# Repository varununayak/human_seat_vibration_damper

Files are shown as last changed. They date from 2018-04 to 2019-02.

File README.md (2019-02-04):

# human_seat_vibration_damper
Design, fabrication, simulation and testing of a viscous dash-pot for a car seat vibration setup. 

This was a project that Varun worked on during his junior year of undergraduate studies at BITS Pilani, Goa Campus, in 2016-17.

Please have a look at the Documentation for theoretical foundations and the design. 

'ENDSemReport3-2.pdf' contains the piston and the vibration setup design (along with the electrodynamic shaker and the sensor-DAQ system) used for the system identification of a passive damper. This design project was further extended to create our very own magnetorhelogical damper. The report also lists three (unsuccessful) attempts to design and fabricate one.

'HumanSeatVibration.pdf' is a short assignment, as part of a course on vibrations and control, that models the dynamics of a seated human body and finds the resonant frequencies and mode shapes of excitation.

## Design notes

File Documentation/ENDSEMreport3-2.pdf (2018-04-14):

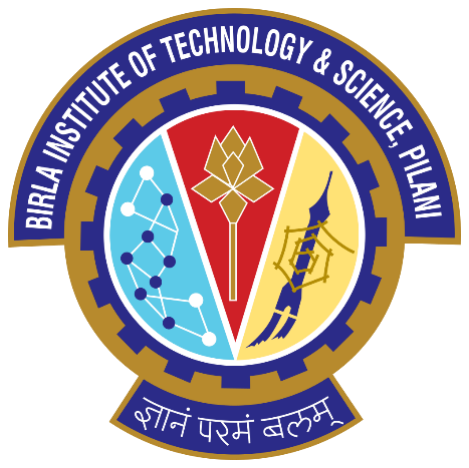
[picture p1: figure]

# SEMESTER REPORT

on

### “System Identification of MR Damper”

Prepared by
Nayak Varun Uday | 2014A4PS086G
Rishabh Chaturvedi | 2014A4PS298G
Shubhan Parag Patni | 2014A4PS154G

for

### Dr PM Singru

Department of Mechanical Engineering BITS Pilani K K Birla Goa Campus

# Acknowledgements

We would like to thank Dr PM Singru for his esteemed guidance throughout the course of this project. It has been a great learning experience for us to work under him at the Machine Dynamics Lab, BITS Pilani K K Birla Goa Campus

We would also like to thank the Workshop Instructors and Superintendent Mr Vijay Suryawanshi for their assistance and cooperation. They played a key role in the fabrication of our damper and setup.

# INDEX

i. Design of a cam to generate sinusoidal input vibration for seat ii. Conversion of Passive Damper to MR Damper (Attempt 1)
a. Setup
b. Use of magnetic particles (Magnaflux Spray) iii. Experimentation
a. Procedure
b. Results
c. Inferences
iv. Conversion of Passive Damper to MR Damper (Attempt 2)
a. Magnetic nano-particles
b. Old MR Damper
v. Experimentation
a. Response for Old MR Damper
b. Summary
vi. Conversion of Passive Damper to MR Damper (Attempt 3)
a. Design of a piston around which a current carrying coil can be wrapped
b. New Setup
vii. Experimentation
a. Procedure
b. Results
c. Inferences
viii. Conclusion

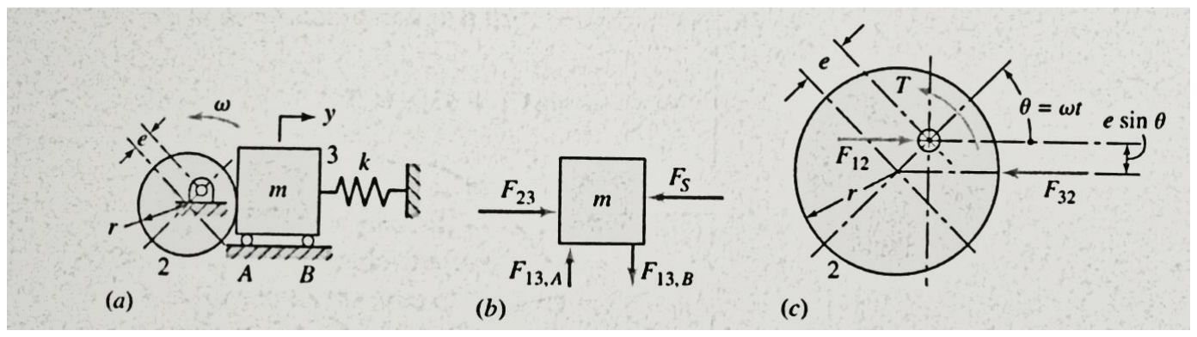
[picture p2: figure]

The CAM follower physical model

### Design of a cam to generate a sinusoidal input for a seat vibration setup

In order to take our studies on human body vibration analysis and ergonomics, we proposed to design a CAM which would generate a sinusoidal input to a seat attached to a follower.

Model-

An eccentric CAM was used as elaborate analytical solutions for its dynamics were available in literature. Also, it would generate the desired sinusoidal oscillatory motion at the output. The CAM would be accompanied by a flat-face follower as this design would be mechanically stronger and less complicated to design and fabricate given the various mechanical elements that are present in a roller follower.

CAM kinematics:

y = e − e cos ωt | ; | ẏ = eω sin ωt | ; | ÿ= eω

2
cos ωt

For the dynamic model, we assume that there is no friction and there is a preload P=kδ where δ is the preload compression given to the follower spring during installation.

Summing forces on the follower mass in the y-direction gives:

| ∑F
y = F23 − k(y + δ) = m ÿ

The force F23 is the contact force between the cam and the follower and hence can have only a positive value. Hence, substitution of the expression for y in the above equation of motion gives

F23 = (mω

2 − k)e cos ωt + (ke + P)

As the maximum probability of contact force becoming zero is at the top of the follower motion (ωt=180°), that value is substituted and F23 is made zero in order to find the value for k (minimum required value is obtained as this is the limiting case).

| | k = mω
| | 2 2e + δ

where

| | m = 100 kg (say) ω = 2π × 5 = 31.4 | rad

s

e = 0.01 cm
δ = 0.01 cm

Thesis values are arbitrary but conservative. Hence, substitution of these values gives:

k = 3287

kN
m

which is a very unrealistic value for a spring.

Let us assume that this spring is available and can be installed. However, we shall see in further calculations that the system parameters are far too unrealistic to be fabricated on the required scale.

Maximum value of F23 occurs at ωt=0, giving

F23(max) ≅ 132 kN

Maximum Torque required

Tmax ≅ 480 N. m

Maximum Power required

P ≅ 15 kW

These values are far too unrealistic to be implemented as anticipated and cannot be implemented with current constraints. As this is the most ideal model, we can safely assume that any other model would produce similar or worse results. The idea of using a cam for a human seat vibration setup is therefore terminated.

### Conversion of Passive Damper to MR Damper (Attempt 1)

Setup

To convert passive damper into active damper we required two modifications in our passive damper.

- To produce uniform magnetic field inside the cylinder of damper. This was achieved by using the basic principle of solenoid, electric current through the coil creates uniform magnetic field inside the coil. For this, we wound the outside of cylinder of damper with wire.

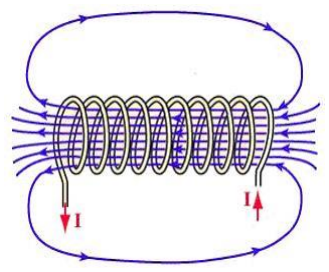
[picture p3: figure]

(Solenoid Magnetic Field)

Strength of magnetic field inside a solenoid is given by:

B =

μNI
L

B: Magnetic field.

µ: Permeability.

N: Number of coil turns (16 number of coil turns for our damper).

I: Current flowing through coil.

L: Length of coil (6cm for our damper).

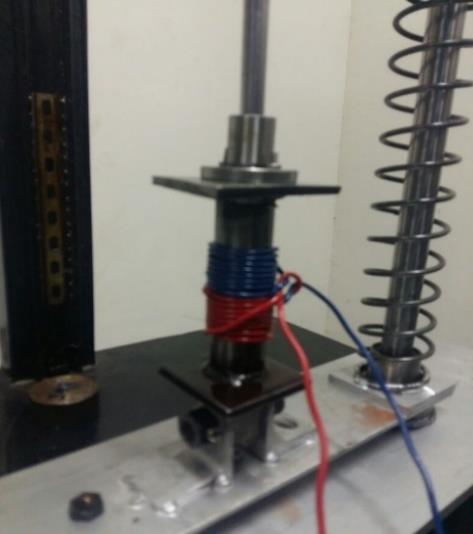
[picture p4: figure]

(Passive Damper converted to MR Damper)

Use of Magnaflux Spray

Secondly, the oil used inside the cylinder should be magnetized so that when it experiences magnetic field, there is change in viscosity of oil. For this purpose, Magnaflux spray used in Magnetic particle inspection for cracks and creeps was mixed with SAE-40 oil which is used in our passive damper and different concentrations of magnetized oil were prepared.

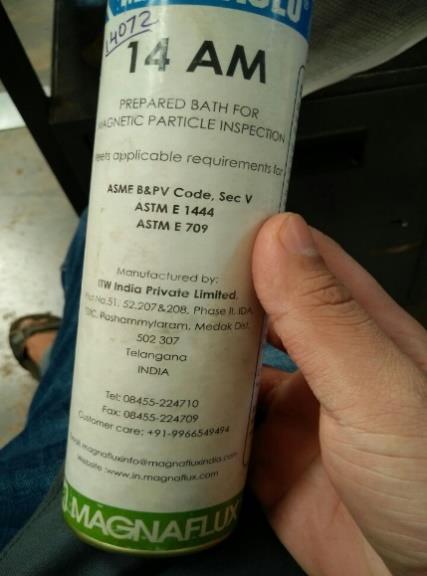
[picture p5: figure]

(Magnaflux Spray)

This kind of MR damper can be reverted back to passive damper anytime whenever required.

### Experimentation

MR dampers, like all magnetic materials, must possess a hysteresis curve. This curve can be represented between the current provided to the MR fluid, and its viscosity. Since the damping coefficient of a damper is directly proportional to the viscosity of the fluid inside it:

c = μ [
3πD

3
l
4d

3

(1 +

2d
D

)]

C is the damping coefficient, µ is the viscosity D, d and l are damper dimensions

A change in the current must produce corresponding changes in the damping provided by the damper. This is taken as a sufficient condition for the success of the experiment.

PROCEDURE

- Magnaflux-14 AM was added to SAE 40 Oil. All concentrations are measured as Wt./Wt. % The standard weight of oil taken = 118.27 g.
- Three concentrations were prepared. The shaker test was carried out for each of these currents while passing different amounts of current through a coil wrapped around the damper cylinder.
- A sine sweep test was carried out from 5Hz to 30Hz using constant displacement input from the shaker = 2 mm.

### 8.4% Magnaflux in SAE 40 Oil

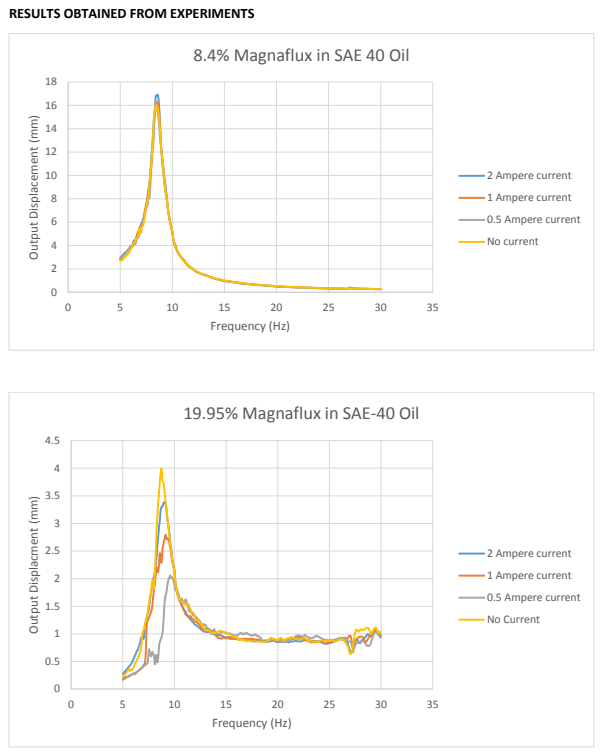
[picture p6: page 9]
Frequency (Hz); 2 Ampere current; 1 Ampere current; 0.5 Ampere current; No current; No Current

RESULTS OBTAINED FROM EXPERIMENTS

Output Displacement (mm)

19.95% Magnaflux in SAE-40 Oil

Output Displacment (mm)

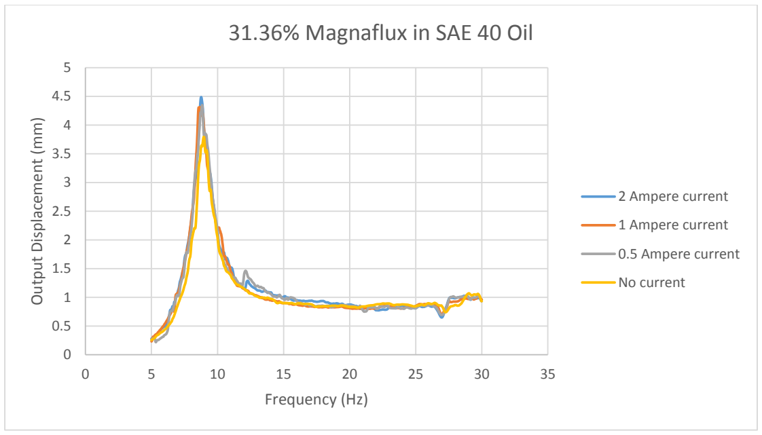
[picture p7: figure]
Output Displacement (mm); Frequency (Hz); 31.36% Magnaflux in SAE 40 Oil; 2 Ampere current; 1 Ampere current; 0.5 Ampere current; No current

INFERENCES

- No substantial change can be seen in the resonating frequencies of the system upon changing the current.
- Similarly, no change is observed in the resonating frequency upon change in concentration.
- There should have been a change in the resonating frequency if the damping of the system was changing due to varying currents. Therefore we can conclude that the damper, upon addition of Magnetic Inspection fluid, and with current passing around the cylinder, DOES NOT behave as an active MR Damper.
There could have been two major reasons for this failure:
- Magnetic Shielding occurs. Since the coil is wrapped outside the cylinder, the fluid (and therefore the magnetic particles) might be shielded by the effects of the solenoid by the cylinder material (Mild Steel).
- The concentration of magnetic particles might be very low to have any significant effect on the damping. The Magnaflux-14 AM only has a 5% proportion of particles to petroleum suspension. Therefore, when we add a portion of Magnaflux-14 AM to the SAE 40 oil, the proportion of magnetic particles introduced into the oil is very low. Thus, the question arises if there is a particular ‘threshold’ concentration beyond which magnetic particles have a significant effect on the viscosity of the MR fluid.

### Conversion of Passive Damper to MR Damper (Attempt 2)

Magnetic Nano-Particles

Magneto Rheological fluid

Electro-rheological (ER) fluid changes viscosity when an electric current is applied directly to the fluid itself. ER fluid was first invented and patented in the 1940s, and to varying degrees, development has continued ever since. It has been tested in a wide range of applications, from torque converters, clutches (http://www.formula1-dictionary.net/clutch.html) and dampers to synthetic muscles and dampers in powered prosthetic arms and legs. It works, but its shear strength (its resistance to shearing movement) is limited. Despite huge investments in research and development, ER fluid is still far from ready for any practical applications.

Magneto-rheological (MR) fluid on other side has shear strength about 10 times stronger than ER fluid. Invented at the same time as ER fluid, the two have many similarities. Both can use oil, silicone, water or glycol as the base fluid, and both contain polarizable particles suspended in the fluid. Polarizable means the particles can be forced to align in a specific way. These suspended polarizable particles are the basic difference between ER and MR fluids. ER fluid uses particles that polarize when directly exposed to an electric current. MR fluid uses somewhat larger particles of iron that polarize when surrounded by a magnetic field.

Our Approach

Fe³⁺ ions were created using the chemical reaction of Fe(OH)3 and HCL. Two types of Iron particles were used purified iron particles and unpurified iron particles. Three different concentrations were made. One with pure particles having concentration 7.5% by weight of pure iron particles in SAE 40 oil, other with impure iron particles having concentration 8.75% by weight of impure iron particles in SAE 40 oil. These two concentrations were used while conducting test with old model of MR Damper having coil wound around cylinder.

Below are the tables describing the observations made while making the above mixture of magnetized fluid:

Old MR Damper (impure Particles)
weight of empty bottle (g) | 19.87
Bottle + Particles (g) | 22.89
Weight of Particles (g) | 3.02
Weight of Bottle + Oil + Particle (g) | 63.11
Weight of Oil (g) | 40.22
Wt/Wt % of oil | 7.508702

Old MR Damper (Pure iron particles)
Empty Bottle Weight (g) | 21.07
Bottle + Particles (g) | 22.17
Particle Wt. (g) | 1.1
Bottle + Particles + Oil (g) | 34.74
Oil (g) | 12.57
Wt./Wt. % | 8.750994

### Experimentation

Test 1: 7.5% wt/wt rough nanoparticles

Sweep Sine Responses for the above concentration are given below.

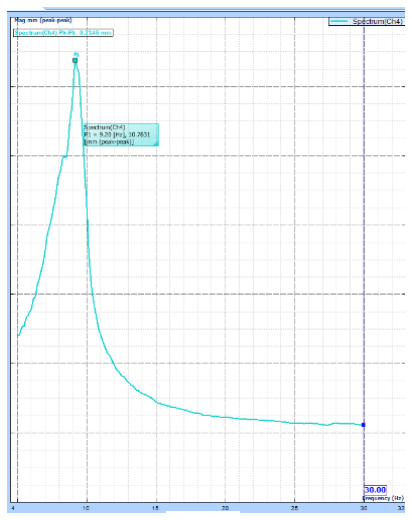
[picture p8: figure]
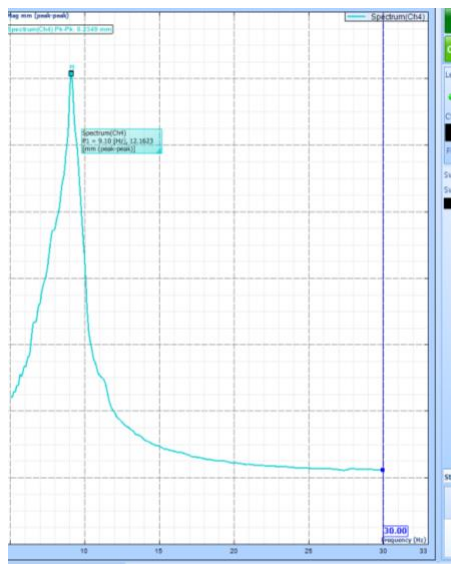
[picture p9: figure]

0A | 0.5A

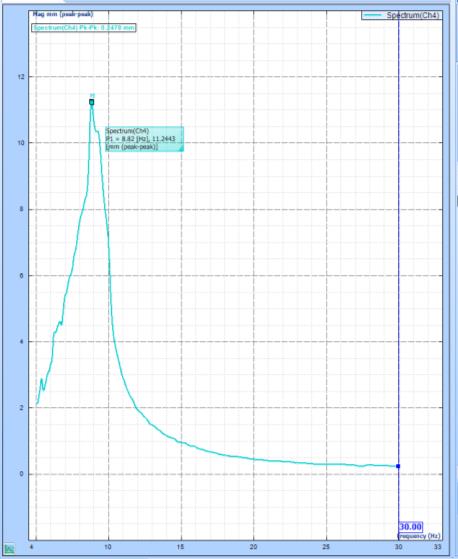
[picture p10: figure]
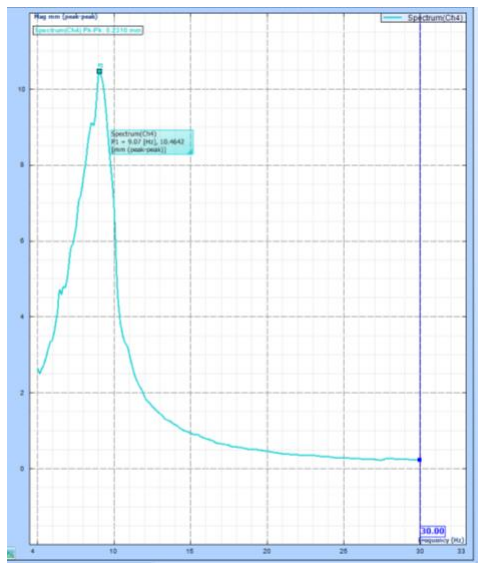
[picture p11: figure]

1A | 2A

Test 2: 8.75% wt/wt rough nanoparticles

Sweep Sine Responses for the above concentration are given below.

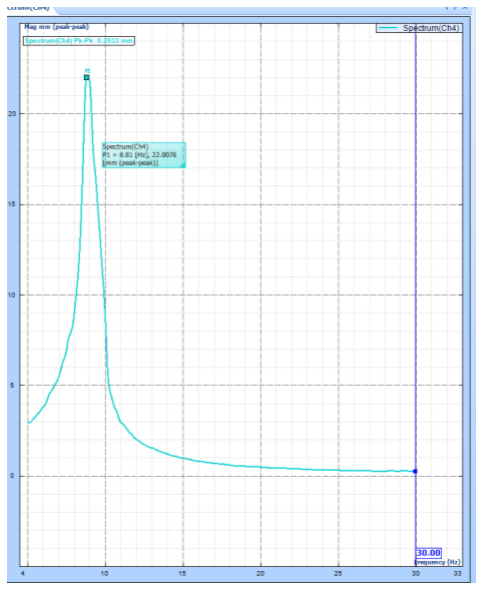
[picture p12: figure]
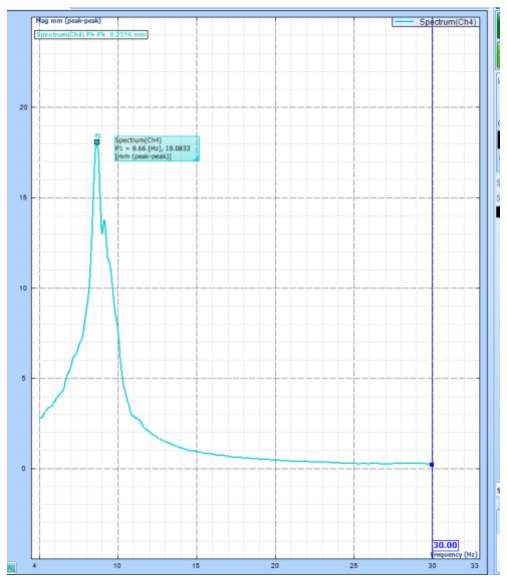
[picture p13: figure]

0A | 0.5A

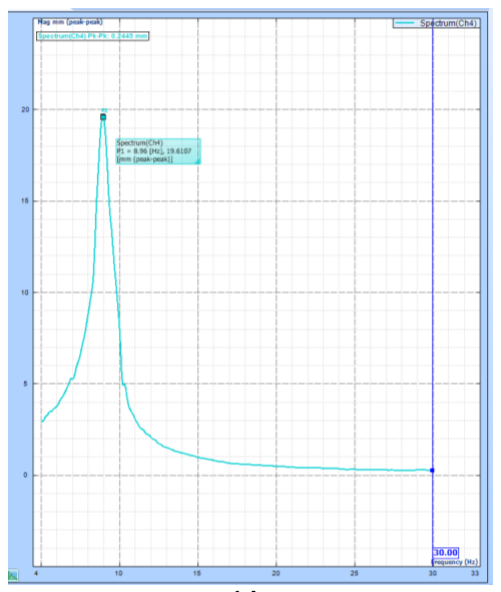
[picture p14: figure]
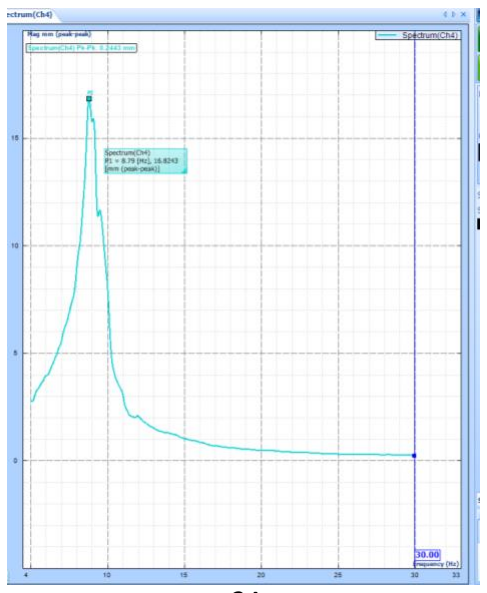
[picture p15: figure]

1A | 2A

Summary of Results

For the old MR damper setup and nano particles, following were the results.:

Current | Unrefined Particles | Refined Particles
0 Ampere | 9.2 Hz | 8.66 Hz
0.5 Ampere | 9.1 Hz | 8.81 Hz
1 Ampere | 8.8 Hz | 8.96 Hz
2 Ampere | 9.07 Hz | 8.79 Hz

### Conversion of Passive Damper to MR Damper (Attempt 3)

Design of a piston around which current-carrying coil can be wrapped

By our current experimentation with the new mixture of oil and magnetic particles, there has been no change in the damping constant of the system for current varying between 0-2A. Therefore, there is a possibility that the magnetic field experienced by the fluid is not strong enough due to the shielding effect of the steel cylinder.
Thus, a new design of the piston in which the current-carrying coil would be wrapped around the piston was to be created.

Points to be taken care of for this design-

1. The groove made in the piston should be of appropriate dimensions so that the piston surface is kept as flat as possible. The safe wire diameter required for this specified order of current is about 0.8 to 1.2mm. Hence the groove depth was decided to be fixed at 1mm.
2. Since there will be wiring coming out of the inside of the cylinder, there should be appropriate arrangements in the sealing made for the same.
3. Overall sealing should be made tight as magnetic nanoparticles are expensive and leakage cannot be afforded. The need for sealing was eliminated in this iteration of design by extending the piston further into the cylinder hence keeping a healthy clearance (about 2cm more than the passive damper) between the upper surface of the fluid and the cylinder opening.

The piston outer diameter was fixed at 17mm and shaft diameter at 10mm (following the passive damper dimensions).

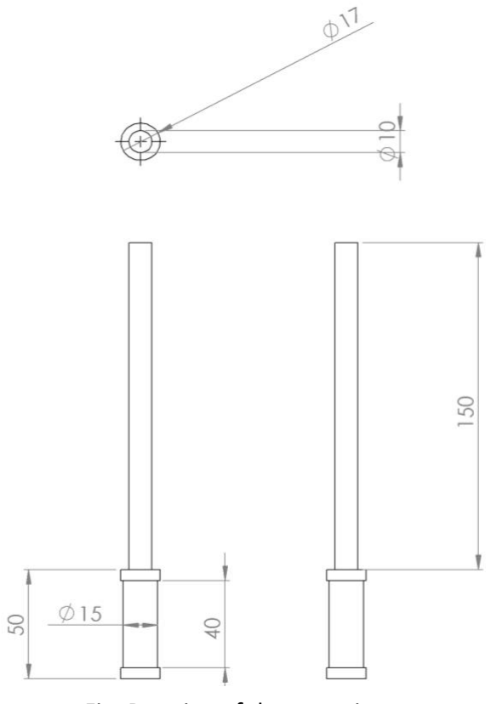
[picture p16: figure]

Fig: Drawing of the new piston

Fabrication of the New Piston

New Piston for the MR Damper was manufactured on Lathe machine carried out in our workshop.

Equipment Used: 25mm MS solid cylinder rod of 30cm length (issued from workshop), Lathe Machine, Vernier Caliper, Flat fine file, Emery paper, 8mm winding wire, feviquick.

Required dimensions of piston: 170mm length of shaft, 50mm length of piston, 10mm diameter of shaft, 17 mm diameter of piston at the ends with 4mm length at each end, middle part of piston is made to be of 15.8mm diameter with its length to be 42mm.

10mm diameter of shaft passes through the linear bearing to keep it centric with the cylinder and tight fits into the upper connector which has hole for the same of 10mm depth 10mm diameter. Linear bearing is screwed on the upper plate of cylinder containing magnetized fluid.

Procedure followed for manufacturing:

- 30mm MS solid cylinder rod of 300mm length is taken a 5mm hole is drilled at one of the faces of MS rod so as to reduce the wobbling by holding the rod in chuck and tailstock of Lathe machine.
- Carrying out the turning operation to reduce diameter from 25 mm to 17mm for 240mm of length of work piece from one end.
- Further carrying out turning operation to reduce 17mm diameter to 10mmdiameter for 180mm of length from the same end.
- To get the middle part of piston from 17mm to 15.8mm, it is machined from 184mm to 234mm from the same end.
- Parting tool is used on both the ends to get the final length of piston and shaft to 220mm as required.
- Winding wire was wound around the middle part of piston with 64 turns.
- Feviquick was used to make sure winding wire is glued to piston and doesn’t loosen up.
- Two ends of the winding wires come out from one of the screw holes of linear bearing out of the cylinder.
Dimension | DESIGN (mm) | ACTUAL (mm)
Piston Diameter (inner) | 15 | 15.4
Piston Diameter (outer) | 17 | 17.1

Table: Piston Dimensions

Setup

For new MR Damper 6.04% by weight of pure iron particles in SAE 40 oil was used. Multiple readings were taken for different value of the current 0, 0.5, 1, 1.5, 2 Amperes.

New MR Damper (Pure iron particles)
Weight of empty bottle(g) | 19.18
Weight of bottle + oil(g) | 75.28
Weight of bottle + oil + particles(g) | 78.67
Weight of Oil(g) | 56.1
Weight of Particles(g) | 3.39
Concentration Wt/Wt(%) | 6.042781

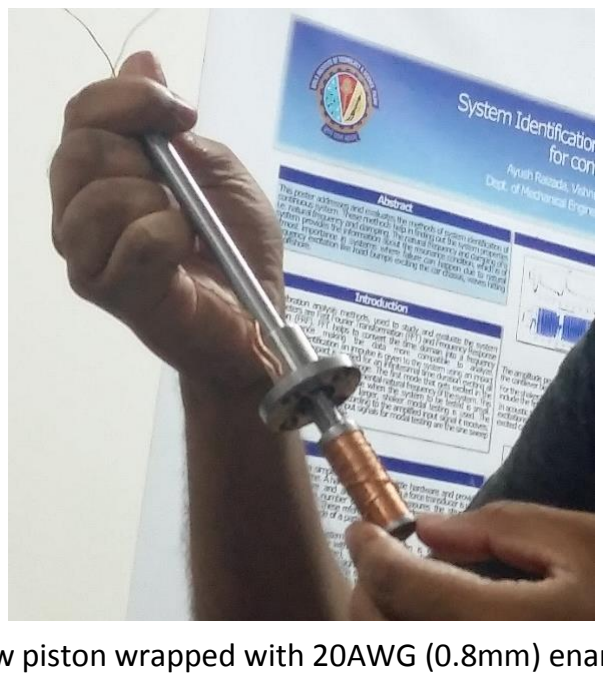
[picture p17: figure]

Fig: The new piston wrapped with 20AWG (0.8mm) enamelled wire

### Experimentation

### No Current

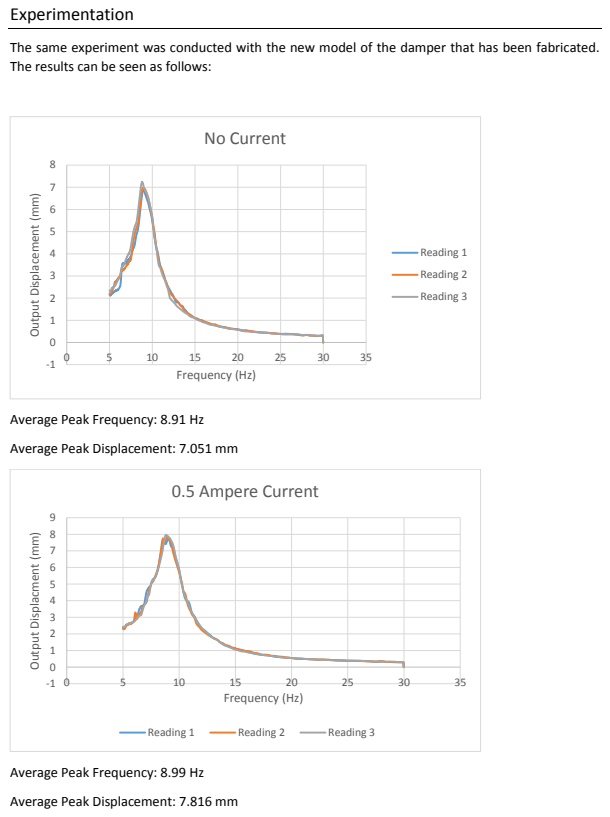
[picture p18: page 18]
Frequency (Hz); Reading 1; Reading 2; Reading 3; 0.5 Ampere Current

The same experiment was conducted with the new model of the damper that has been fabricated.
The results can be seen as follows:

Output Displacement (mm)

Average Peak Frequency: 8.91 Hz

Average Peak Displacement: 7.051 mm

Output Displacment (mm)

Average Peak Frequency: 8.99 Hz

Average Peak Displacement: 7.816 mm

### 1 Ampere Current

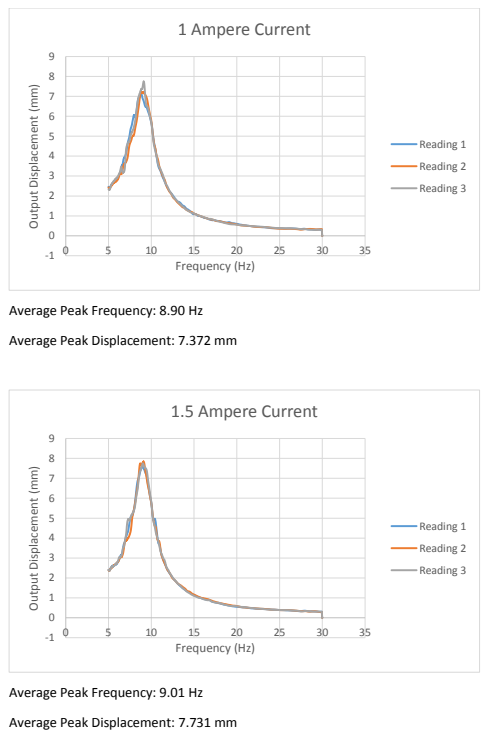
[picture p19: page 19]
Frequency (Hz); Reading 1; Reading 2; Reading 3; 1.5 Ampere Current

Output Displacement (mm)

Average Peak Frequency: 8.90 Hz

Average Peak Displacement: 7.372 mm

Average Peak Frequency: 9.01 Hz

Average Peak Displacement: 7.731 mm

### 1.91 Ampere Current

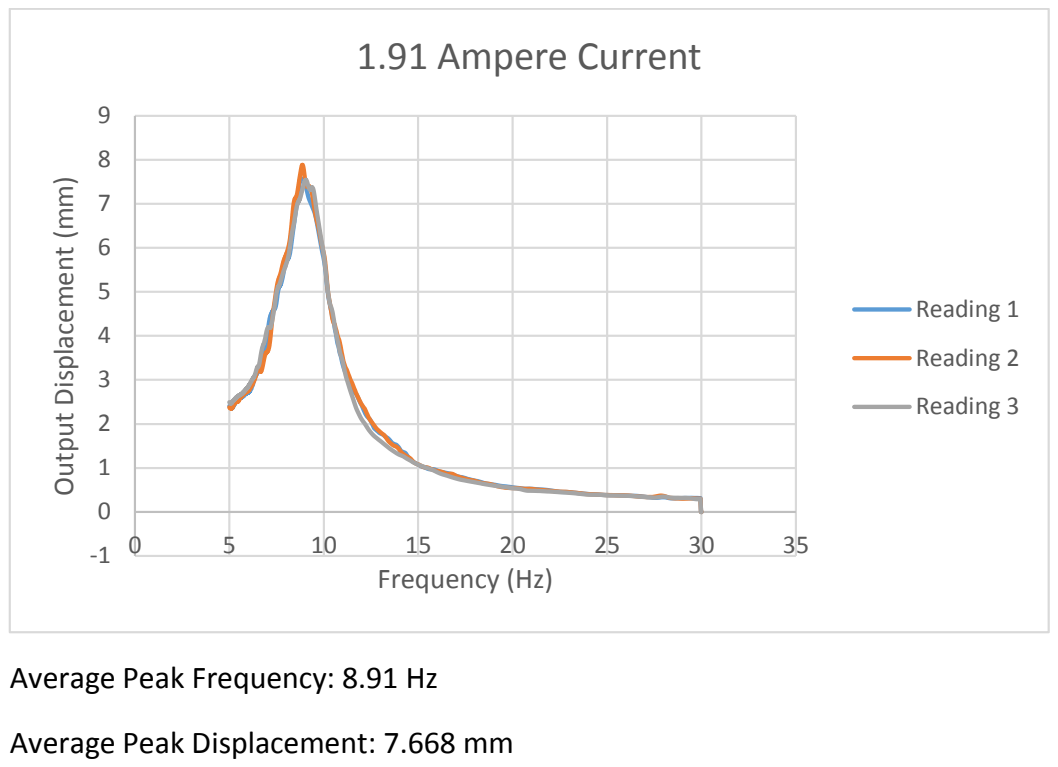
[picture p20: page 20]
Frequency (Hz); Reading 1; Reading 2; Reading 3

Output Displacement (mm)

Average Peak Frequency: 8.91 Hz

Average Peak Displacement: 7.668 mm

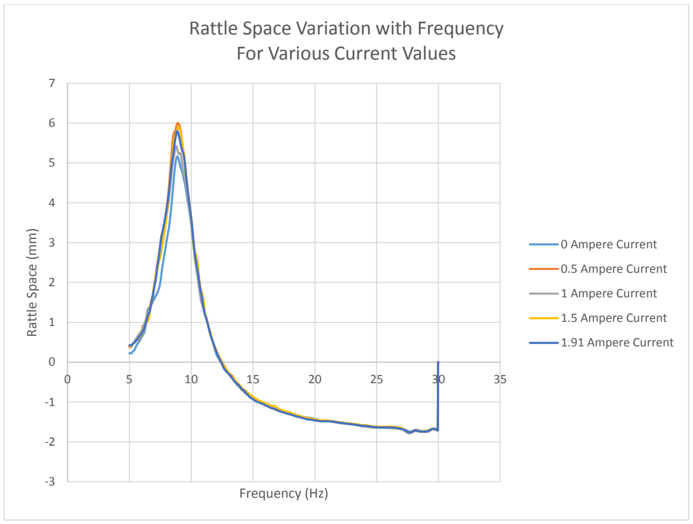
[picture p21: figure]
Rattle Space (mm); Frequency (Hz); Rattle Space Variation with Frequency For Various Current Values; 0 Ampere Current; 0.5 Ampere Current; 1 Ampere Current; 1.5 Ampere Current; 1.91 Ampere Current

Although there is slight variation of the resonant frequency, it is not uniform, nor can any predictable pattern be observed. The variation can simply be attributed to arise from experimental errors, which would not be present in an ideal scenario. Thus the attempt to construct an inexpensive MR Damper has failed.

Possible Reasons for failure:

1. The ferromagnetic particles are heavy. They do not float in the oil but rather settle down to the bottom of the cylinder and therefore no effect can be observed on the fluid’s viscosity.
2. The number of turns on the piston may not be enough to generate a field strong enough to magnetise the fluid and affect its viscosity.

Further:

A surfactant such as oleic acid, or more commonly a detergent, can be added to the oil. This will increase the surface tension of the fluid and prohibit the particles from settling down.

Better methods for obtaining/purifying of particles can be used so that the particles are finer and lighter.

### Conclusion

After successfully designing, fabricating and testing the passive damper, the objective of this semester’s work was to design and fabricate a low-cost active damper. After gathering the required materials and exhaustive experimentation, a total of three attempts were possible in the stipulated time. Unfortunately, the results indicate that the attempts were unsuccessful.

However, there still exists a good possibility of ensuring active response from the setup by following the suggestions mentioned above as well as further research on MR damper technology.

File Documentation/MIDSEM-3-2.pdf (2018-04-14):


# MID-SEMESTER REPORT

on

### “System Identification of MR Damper”

Prepared by
Nayak Varun Uday | 2014A4PS086G
Rishabh Chaturvedi | 2014A4PS298G
Shubhan Parag Patni | 2014A4PS154G

for

### Dr PM Singru

Department of Mechanical Engineering BITS Pilani K K Birla Goa Campus

# INDEX

i. Design of a cam to generate sinusoidal input vibration for seat
ii. | Conversion of Passive Damper to MR Damper
iii. | Attempt to convert passive damper to active damper by introduction of magnetic particles in damper oil
a. Procedure
b. Results
c. Inferences
d. Further Iterations
iv. Design of a piston around which a current carrying coil can be wrapped


The CAM follower physical model

### Design of a cam to generate a sinusoidal input for a seat vibration setup

In order to take our studies on human body vibration analysis and ergonomics, we proposed to design a CAM which would generate a sinusoidal input to a seat attached to a follower.

Model-

An eccentric CAM was used as elaborate analytical solutions for its dynamics were available in literature. Also, it would generate the desired sinusoidal oscillatory motion at the output. The CAM would be accompanied by a flat-face follower as this design would be mechanically stronger and less complicated to design and fabricate given the various mechanical elements that are present in a roller follower.

CAM kinematics:

y = e − e cos ωt | ; | ẏ = eω sin ωt | ; | ÿ= eω

2
cos ωt

For the dynamic model, we assume that there is no friction and there is a preload P=kδ where δ is the preload compression given to the follower spring during installation.

Summing forces on the follower mass in the y-direction gives:

| ∑F
y = F23 − k(y + δ) = m ÿ

The force F23 is the contact force between the cam and the follower and hence can have only a positive value. Hence, substitution of the expression for y in the above equation of motion gives

F23 = (mω

2 − k)e cos ωt + (ke + P)

As the maximum probability of contact force becoming zero is at the top of the follower motion (ωt=180°), that value is substituted and F23 is made zero in order to find the value for k (minimum required value is obtained as this is the limiting case).

| | k = mω
| | 2 2e + δ

where

| | m = 100 kg (say) ω = 2π × 5 = 31.4 | rad

s

e = 0.01 cm
δ = 0.01 cm

Thesis values are arbitrary but conservative. Hence, substitution of these values gives:

k = 3287

kN
m

which is a very unrealistic value for a spring.

Let us assume that this spring is available and can be installed. However, we shall see in further calculations that the system parameters are far too unrealistic to be fabricated on the required scale.

Maximum value of F23 occurs at ωt=0, giving

F23(max) ≅ 132 kN

Maximum Torque required

Tmax ≅ 480 N. m

Maximum Power required

P ≅ 15 kW

These values are far too unrealistic to be implemented as anticipated and cannot be implemented with current constraints. As this is the most ideal model, we can safely assume that any other model would produce similar or worse results. The idea of using a cam for a human seat vibration setup is therefore terminated.

### Conversion of Passive Damper to MR Damper

To convert passive damper into active damper we required two modifications in our passive damper.

- Firstly, to produce uniform magnetic field inside the cylinder of damper. This was achieved by using the basic principle of solenoid, electric current through the coil creates uniform magnetic field inside the coil. For this, we wound the outside of cylinder of damper with wire.

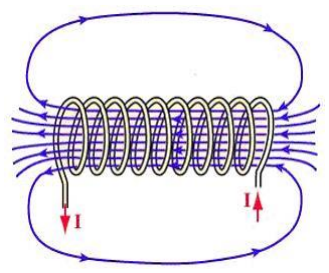
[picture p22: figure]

(Solenoid Magnetic Field)

Strength of magnetic field inside a solenoid is given by:

B =

μNI
L

B: Magnetic field.

µ: Permeability.

N: Number of coil turns (16 number of coil turns for our damper).

I: Current flowing through coil.

L: Length of coil (6cm for our damper).

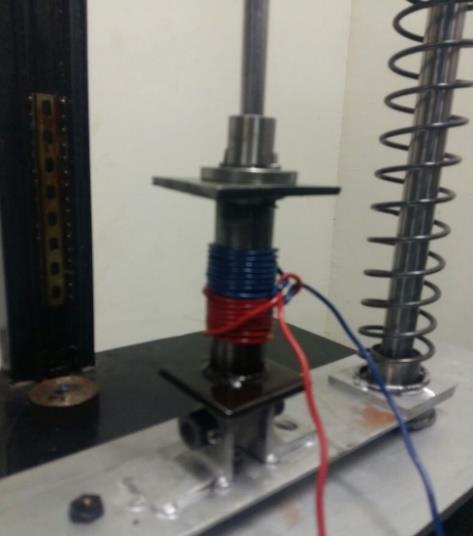
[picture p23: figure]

(Passive Damper converted to MR Damper)

- Secondly, the oil used inside the cylinder should be magnetized so that when it experiences magnetic field, there is change in viscosity of oil. For this purpose, Magnaflux spray used in

Magnetic particle inspection for cracks and creeps was mixed with SAE-40 oil which is used in our passive damper and different concentrations of magnetized oil were prepared.


(Magnaflux Spray)

This kind of MR damper can be reverted back to passive damper anytime whenever required.

Problem with this MR Damper

- There is a possibility that cylinder’s thickness will shield the magnetic field produced inside the cylinder. We haven’t been able to confirm that magnetic shielding exists and if it exists then what is the strength of magnetic field produced inside the cylinder.
- It cannot be assured that mixing SAE 40 oil with Magnaflux spray will result in magnetized oil.

Alternative approach

To encounter the problem that exists with this revertible MR damper this alternative approach is being considered.

- We need to manufacture another piston onto which the wire will be wound around as done in standard MR dampers this will eliminate shielding of magnetic field.
- SAE 40 oil can be mixed with Nano magnetic particles to get magnetized oil for MR damper.

### Experiment: Attempt to convert passive damper to active damper by

introduction of Magnetic Particles into damper oil.

MR dampers, like all magnetic materials, must possess a hysteresis curve. This curve can be represented between the current provided to the MR fluid, and its viscosity. Since the damping coefficient of a damper is directly proportional to the viscosity of the fluid inside it:

c = μ [
3πD

3
l
4d

3

(1 +

2d
D

)]

C is the damping coefficient, µ is the viscosity D, d and l are damper dimensions

A change in the current must produce corresponding changes in the damping provided by the damper. This is taken as a sufficient condition for the success of the experiment.

PROCEDURE

- Magnaflux-14 AM was added to SAE 40 Oil. All concentrations are measured as Wt./Wt. % The standard weight of oil taken = 118.27 g.
- Three concentrations were prepared. The shaker test was carried out for each of these currents while passing different amounts of current through a coil wrapped around the damper cylinder.
- A sine sweep test was carried out from 5Hz to 30Hz using constant displacement input from the shaker = 2 mm.

### 8.4% Magnaflux in SAE 40 Oil

Frequency (Hz); 2 Ampere current; 1 Ampere current; 0.5 Ampere current; No current; No Current

RESULTS OBTAINED FROM EXPERIMENTS

Output Displacement (mm)

19.95% Magnaflux in SAE-40 Oil

Output Displacment (mm)

Output Displacement (mm); Frequency (Hz); 31.36% Magnaflux in SAE 40 Oil; 2 Ampere current; 1 Ampere current; 0.5 Ampere current; No current

INFERENCES

- No substantial change can be seen in the resonating frequencies of the system upon changing the current.
- Similarly, no change is observed in the resonating frequency upon change in concentration.
- There should have been a change in the resonating frequency if the damping of the system was changing due to varying currents. Therefore we can conclude that the damper, upon addition of Magnetic Inspection fluid, and with current passing around the cylinder, DOES NOT behave as an active MR Damper.
There could have been two major reasons for this failure:
- Magnetic Shielding occurs. Since the coil is wrapped outside the cylinder, the fluid (and therefore the magnetic particles) might be shielded by the effects of the solenoid by the cylinder material (Mild Steel).
- The concentration of magnetic particles might be very low to have any significant effect on the damping. The Magnaflux-14 AM only has a 5% proportion of particles to petroleum suspension. Therefore, when we add a portion of Magnaflux-14 AM to the SAE 40 oil, the proportion of magnetic particles introduced into the oil is very low. Thus, the question arises if there is a particular ‘threshold’ concentration beyond which magnetic particles have a significant effect on the viscosity of the MR fluid.

FURTHER ITERATIONS

- Introduction of Fe³⁺ particles into the damper oil. As we are directly introducing particles instead of a suspension, the concentration will be sharper.
- Wrapping the current carrying coil inside the damper by wrapping it around the piston. This will help in eliminating magnetic shielding as a reason for no change in the response of the system.

### Design of a piston around which current-carrying coil can be wrapped

By our current experimentation with the new mixture of oil and magnetic particles, there has been no change in the damping constant of the system for current varying between 0-2A. Therefore, there is a possibility that the magnetic field experienced by the fluid is not strong enough due to the shielding effect of steel.

Thus, a new design of the system in which the current-carrying coil will be wrapped around the piston will have to be designed.

Points to be taken care of for this design-

1. The groove made in the piston should be of appropriate dimensions so that the piston surface is kept as flat as possible
2. Since there will be wiring coming out of the inside of the cylinder, there should be appropriate arrangements in the sealing made for the same.
3. Overall sealing should be made tight as magnetic nanoparticles are expensive and leakage cannot be afforded

The project will proceed further with the design, fabrication and testing of the MR Damper equipped with such a piston. However, before we proceed, we will check whether our assumption of shielding is actually true or not by checking the magnetic field developed inside the cylinder with the current design configuration.

Proposed Piston Design

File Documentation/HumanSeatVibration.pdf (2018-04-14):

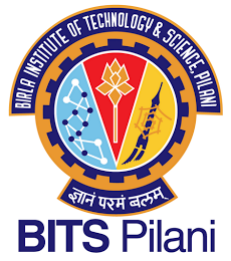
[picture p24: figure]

# Mode Shape Determination of a Dynamic Model of a Human Body in Seated Position

## Varun Uday Nayak ID: 2014A4PS086G

A project presented for partial fulfilment of the requirements of the course Mechanical Vibrations

## Department of Mechanical Engineering BITS Pilani, K K Birla Goa Campus

## Contents

1 Introduction | 2
2 Literature Used | 2
3 Human Body Model | 3
4 Equation of Motion | 4
5 Mode Shapes | 5
6 MATLAB Code | 6
7 Conclusion | 7
8 References | 7

1

## Mode Shape Determination of a Dynamic Model of a Human Body in Seated Position

Varun Uday Nayak
ID Number: 2014A4PS086G

Birla Institute of Technology and Science, Pilani - K K Birla Goa Campus

April 25, 2017

## 1 Introduction

The human body is subject to forces and displacements in everyday life: while one exercises, while one sits inside a moving car, while one performs manual labour and numerous other scenarios. Studying the dynamics of a human body has become an interesting topic of research in domains such as ergonomics, biomechanics, prosthetics, rehabilitation robotics and human-machine interaction. Since the human body is a complicated system, it had always been difficult to model it using simple analytical techniques. With improvements in computational techniques and rapid development in the field of biomechanics, it has become possible to accurately model such systems. Experimental testing has also evolved significantly due to the use of bio-instrumentation and carefully controlled dynamic environments.

## 2 Literature Used

A lot of research has been carried out in the domain of seat vibration models of a human body among other configurations. Behari and Noga [1] have developed five different biodynamic models of a seated human body and have analysed the transmissibility of seat vibrations onto the head. They have provided comprehensive anatomical data and have plotted results that give us an idea of the effect of frequency on the head transmissibility. Amar Kishore et al [3] have also done a transmissibility analysis of a seated human, specifically in the low frequency region. This makes prefect sense for regular car and bus commute on non-ideal roads. The model in this paper has most of its roots in the model presented in their paper due to its simplicity and effectiveness. Ksiazek and Lacny [4] have studied a 2-DOF active human body model with two distinct seat positions and analysed response due to impulse inputs. Liang and Chiang [2] have presented a rather complicated model of a human body considering all possible joints and have tabulated the results for seat-to-head transmissibility like [1] and [3].

2

## 3 Human Body Model


Figure 1: 5-DOF Seated Human Body Biomechanical Model

The human body can be modelled as a 5-DOF system as shown below. Note that as the objective of this paper is to develop a biomechanical model of a human body on a vibrating seat in vertical direction only, the masses have been lumped in a manner which results out of the consideration of only that direction. The abdomen has been assumed to be not connected to the back directly. The lower body and the pelvis have been merged into one to avoid the complexities involving joints in the leg and feet. Also, the feet have been assumed to be placed (fixed) flat on the ground. This model is a a great model for seat vibration analysis of a human body.

3

## 4 Equation of Motion

Applying Force Balance on (1)Pelvis and Lower Body (2)Abdomen (3)Upper Torso (4)Back and (5)Head, we get

m1x¨1 + ˙x1(c1 + c2 + c4 + c6) + ˙x2(−c2) + ˙x4(−c4) + x1(k1 + k2 + k4 + k6) + x2(−k2) + x4(−k4) = 0 (1) m2x¨2 + ˙x2(c2 + c3) + ˙x1(−c2) + ˙x3(−c3) + x2(k2 + k3) + x1(−k2) + x3(−k3) = 0 (2) m3x¨3 + ˙x3(c3 + c7) + ˙x2(−c3) + ˙x4(−c7) + x3(k3 + k7) + x2(−k3) + x4(−k7) = 0 (3) m4x¨4 + ˙x4(c4 + c5 + c7) + ˙x3(−c7) + ˙x1(−c4) + ˙x5(−c5) + x4(k4 + k5 + k7) + x3(−k7) + x1(−k4) + x5(−k5) = 0 (4) m5x¨5 + ˙x5(c5) + ˙x4(−c5) + x5(k5) + x4(−k5) = 0 (5)

In matrix form
m1 | 0 | 0 | 0 | 0
0 | m2 | 0 | 0 | 0
0 | 0 | m3 | 0 | 0
0 | 0 | 0 | m4 | 0
0 | 0 | 0 | 0 | m5

X¨ +

c1 + c2 + c4 + c6 | −c2 | 0 | −c4 | 0
−c2 | c2 + c3 | −c3 | 0 | 0
0 | −c3 | c3 + c7 | −c7 | 0
−c4 | 0 | −c7 | c4 + c5 + c7 | −c5
0 | 0 | 0 | −c5 | c5

X˙

+

k1 + k2 + k4 + k6 | −k2 | 0 | −k4 | 0
−k2 | k2 + k3 | −k3 | 0 | 0
0 | −k3 | k3 + k7 | −k7 | 0
−k4 | 0 | −k7 | k4 + k5 + k7 | −k5
0 | 0 | 0 | −k5 | k5

X = 0

(6)
Assuming the solution xi = Aie st and substituting it into (6), we get

m1s

2 + (c1 + c2 + c4 + c6)s + (k1 + k2 + k4 + k6) | −c2s − k2 | 0
−c2s − k2 | m2s
| 2 + (c2 + c3)s + k2 + k3 | −c3s − k3
0 | −c3s − k3 | m3s 2 + (c3 + c7)s + k3 + k7
−c4s − k4 | 0 | −c7s − k7
0 | 0 | 0
−c4s − k4 | 0
0 | 0
−c7s − k7 | 0
m4s
2 + (c4 + c5 + c7)s + k4 + k5 + k7 | −c5s − k5
−c5s − k5 | m5s 2 + c5s + k5

= 0 | (7)

4

## 5 Mode Shapes

The amplitude of the pelvis and lower body lumped mass is taken to be of unit magnitude while plotting the mode shapes. Using MATLAB, the mode shapes thus obtained are shown in the figure below.


Figure 2: Mode Shapes for the Five Distinct Modes
Note: Point No. 5 for mode1 with an amplitude of about 160, is not shown in graph

5

## 6 MATLAB Code

The MATLAB code contains two different functions. (1)To calculate the five complex frequencies and plot the mode shape using the values of amplitudes after solving the linear equations and (2)To call the plotting function five times for the five modes.

f u n c ti o n S oln=thehuman ( i )
%%HUMAN BODY MODE SHAPE PLOTTER%%
%%AUTHOR VARUN UDAY NAYAK%%
m1=28;m2=6;m3= 2 8. 5;m4=7;m5= 5. 4;
k1=0;k2=187000; k3=208000; k4=250000; k5=310000; k6=103000; k7=183000; c1=0; c2 =5190; c3 =5400; c4 =3585; c5 =1400; c6 =2370; c7 =2850;
syms s ;
A=[m1∗ s ˆ2+( c1+c2+c4+c6 ) ∗ s+(k1+k2+k4+k6 ) ,−c2 ∗s−k2 ,0 , − c4 ∗s−k4 ,0; − c2 ∗s−k2 , m2∗ s ˆ2+( c2+c3 ) ∗ s+k2+k3,−c3 ∗s−k3 , 0 , 0; 0 , − c3 ∗s−k3 ,m3∗ s ˆ2+( c3+c7 ) ∗ s+k3+ k7,−c7 ∗s−k7 ,0; − c4 ∗s−k4 ,0 , − c7 ∗s−k7 ,m4∗ s ˆ2+( c4+c5+c7 ) ∗ s+k4+k5+k7,−c5 ∗s −k5 ; 0 , 0 , 0 , − c5 ∗s−k5 ,m5∗ sˆ2+c5 ∗ s+k5 ] ;
R=de t (A) ;
S=s i m p l i f y (R) ;
d=vpa ( s o l v e (S , ’ s ’ ) ) ;
s v a l u e s =[s q r t (d ( 1 ) ∗d ( 2 ) ) , s q r t (d ( 3 ) ∗d ( 4 ) ) , s q r t (d ( 5 ) ∗d ( 6 ) ) , s q r t (d ( 7 ) ∗d ( 8 ) ) , s q r t (d ( 9 ) ∗d ( 1 0 ) ) ] ;
syms a2 a3 a4 a5 ;
B=[ 1; a2 ; a3 ; a4 ; a5 ] ;
syms C;
C=A∗B;
C=sub s (C, s , s v al u e s ( i ) ) ; D= [ 0 ; 0 ; 0 ; 0 ; 0 ] ;
eqn1=C( 1 ) ==0;
eqn2=C( 2 ) ==0;
eqn3=C( 3 ) ==0;
eqn4=C( 4 ) ==0;
s o l = s o l v e ( [ eqn1 , eqn2 , eqn3 , eqn4 ] , [ a2 , a3 , a4 , a5 ] ) ; c=z e r o s ( 1 , 5 ) ;
c ( 1 ) =1;
c ( 2 )=d ouble ( s o l . a2 ) ;
c ( 3 )=d ouble ( s o l . a3 ) ; c ( 4 )=d ouble ( s o l . a4 ) ; c ( 5 )=d ouble ( s o l . a5 ) ; t = 1: 1: 5;
pl o t (t , c ) ;
ylim ( [ 0 , 2 0 ] ) ;
xlim ( [ 1 5 ] ) ;
end

6

## 7 Conclusion

Therefore, we see that the mode shapes give vital information regarding the response of a seated human body. The effect on the head (X5) is seen evidently as there is a significant difference in its amplitude for different frequency ranges. The pelvis (X1), abdomen (X2) and upper torso (X3) seem to vibrate closer in phase with each other as seen from the mode shapes. All in all, this model gives a fairly accurate idea of the dynamic behaviour of a human body under seat-vibration conditions.

## 8 References

1. Behari N., Noga M., Vibration Transmissibility Behaviour of Simple Biodynamic Models used in Vehicle Seat Design, Technical Transactions Mechanika, 5-M/2016
2. Liang C., Chiang C., Modelling of a Seated Human Body Exposed to Vertical Vibrations in Various Automotive Postures, Industrial Health 2008 46, 125-127, 2008
3. NV Amar Kishore et al, Transmissibility and DPMI analysis of the seated posture of Human under Low frequency vibration, Mechanical and Industrial Engineering Department, Indian Institute of Technology, Roorkee
4. Kisazek M, Lacny L, A Comparison of the Human Body Seat Model Responses to Several Types of Impulse Excitations, Journal of Theoretical and Applied Mechanics, 52, 3, pp. 839-845, Warsaw 2014

7

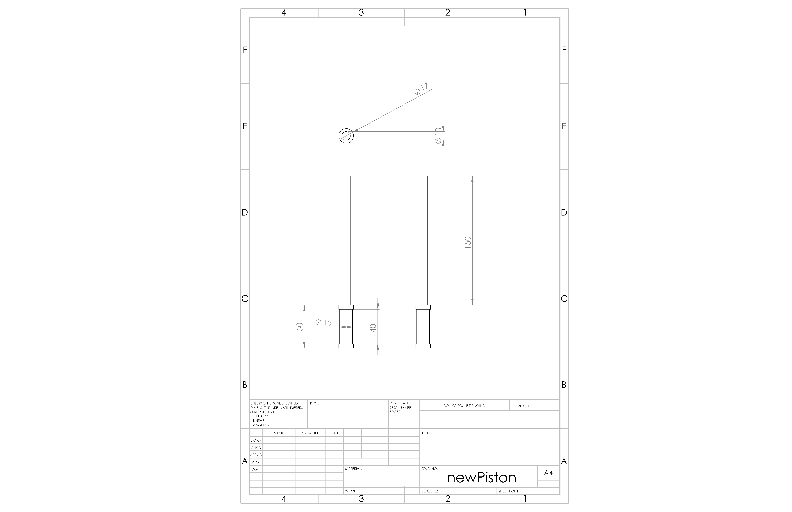
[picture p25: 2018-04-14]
CAD Files/PistonDesign for Custom MR Damper/newPiston.JPG

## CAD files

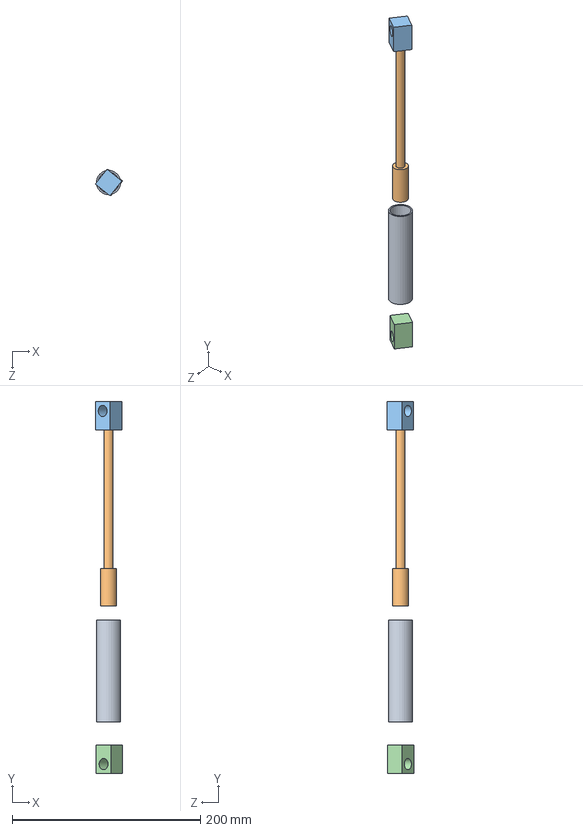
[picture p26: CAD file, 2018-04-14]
CAD Files/ViscousDashpotPartsAug2016/Dashpot_v2/Assem1.SLDASM
29.1 x 394.8 x 28.1 mm
Piston
upperconnector
lowerconnector

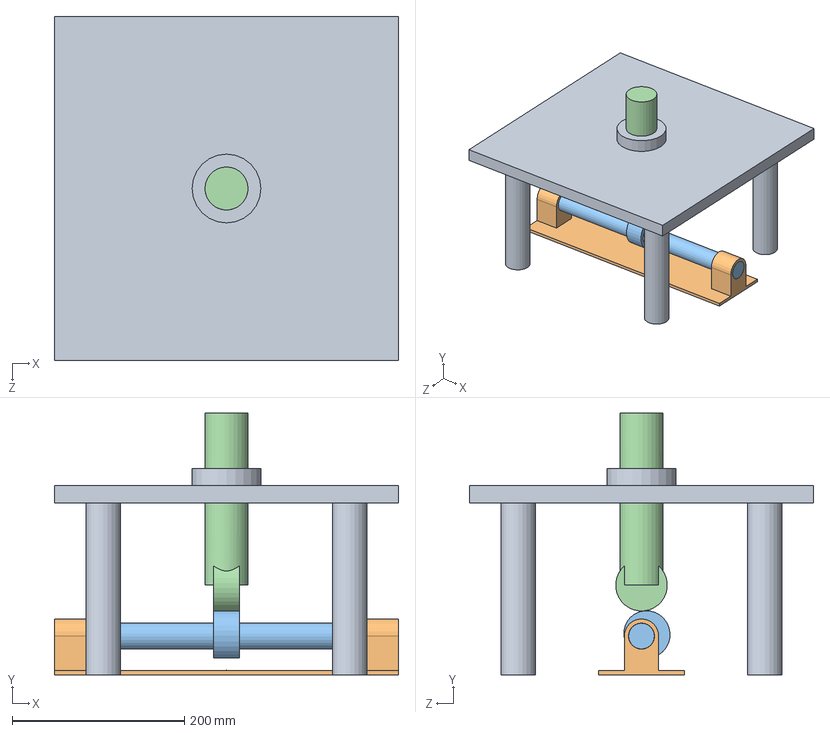
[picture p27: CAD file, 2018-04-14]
CAD Files/Cam-Follower SLDPARTS/CAM Follower.SLDASM
400.0 x 304.2 x 400.0 mm
stoolsupp
basebearings
CAM
follower

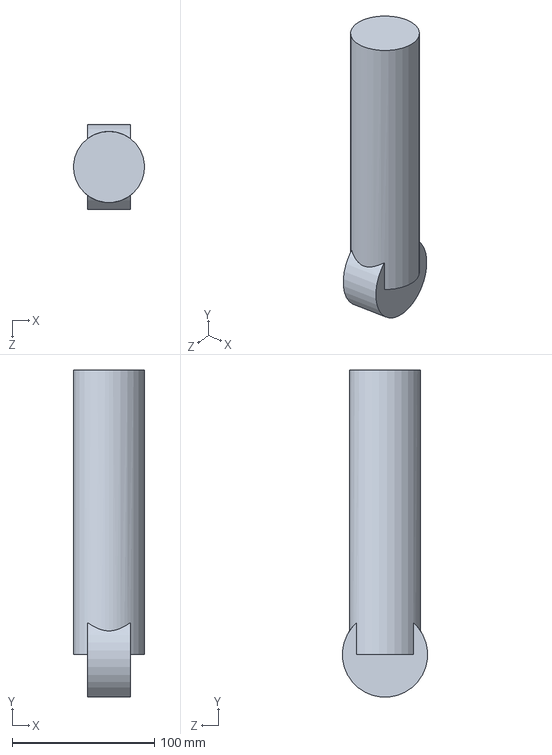
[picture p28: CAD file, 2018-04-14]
CAD Files/Cam-Follower SLDPARTS/follower.SLDPRT
49.9 x 229.9 x 59.8 mm

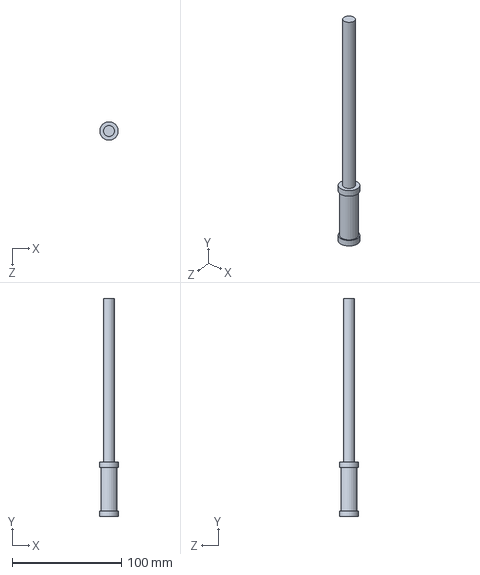
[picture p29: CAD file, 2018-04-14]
CAD Files/PistonDesign for Custom MR Damper/newPiston.SLDPRT
17.0 x 200.0 x 17.0 mm

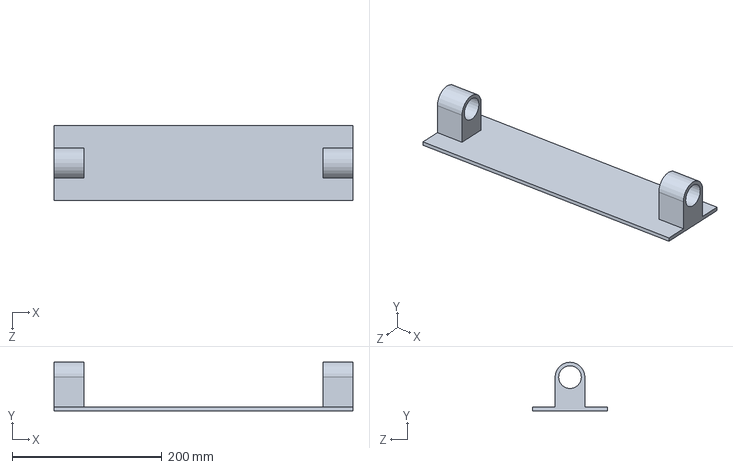
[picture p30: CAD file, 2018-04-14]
CAD Files/Cam-Follower SLDPARTS/basebearings.SLDPRT
400.0 x 65.0 x 100.0 mm

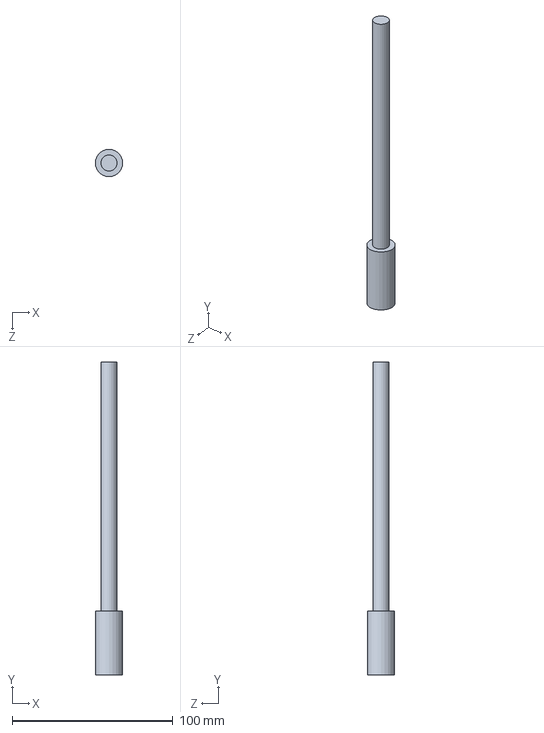
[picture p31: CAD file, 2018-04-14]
CAD Files/ViscousDashpotPartsAug2016/Dashpot_v2/Piston.SLDPRT
17.0 x 195.0 x 17.0 mm

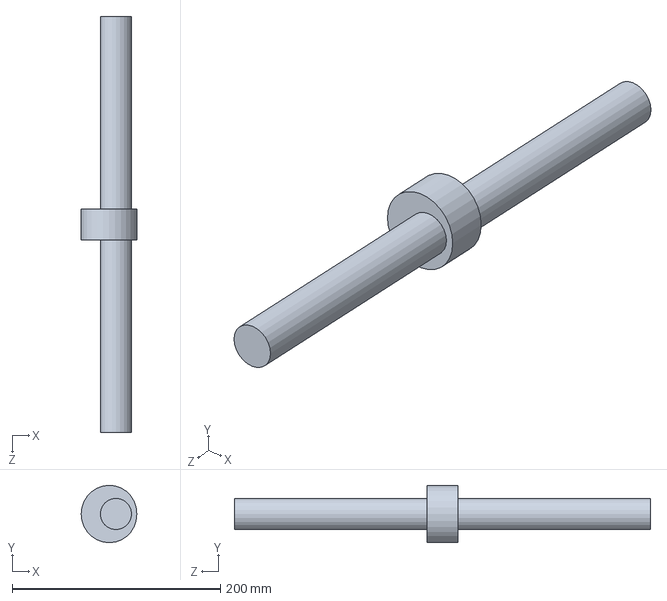
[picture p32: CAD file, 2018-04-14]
CAD Files/Cam-Follower SLDPARTS/CAM.SLDPRT
53.6 x 55.2 x 400.0 mm

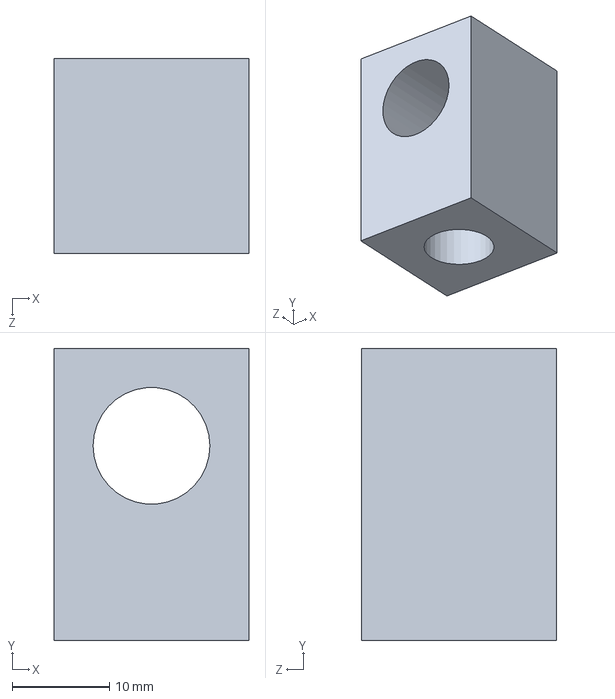
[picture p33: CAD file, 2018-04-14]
CAD Files/ViscousDashpotPartsAug2016/Dashpot_v2/upperconnector.SLDPRT
20.0 x 30.0 x 20.0 mm

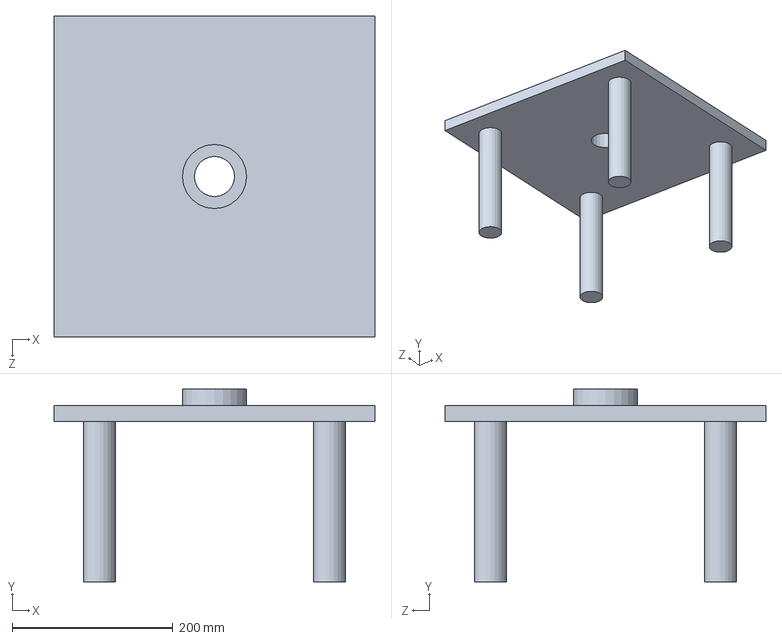
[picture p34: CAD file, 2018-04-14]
CAD Files/Cam-Follower SLDPARTS/stoolsupp.SLDPRT
400.0 x 240.0 x 400.0 mm

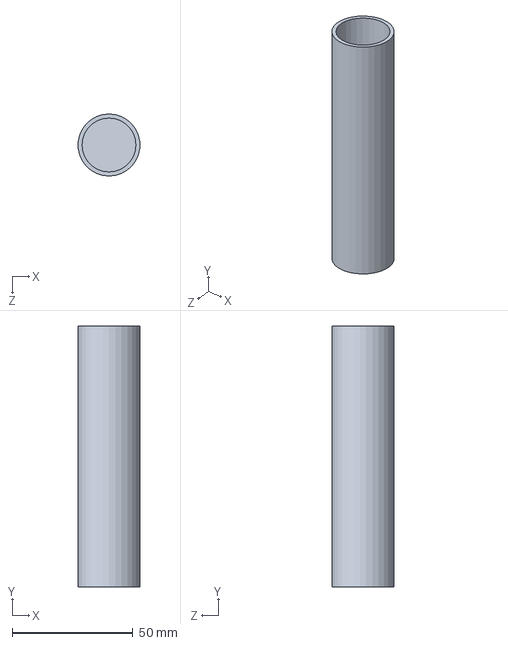
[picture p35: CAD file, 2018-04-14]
CAD Files/ViscousDashpotPartsAug2016/Dashpot_v2/Cylinder.SLDPRT
25.6 x 108.0 x 25.7 mm

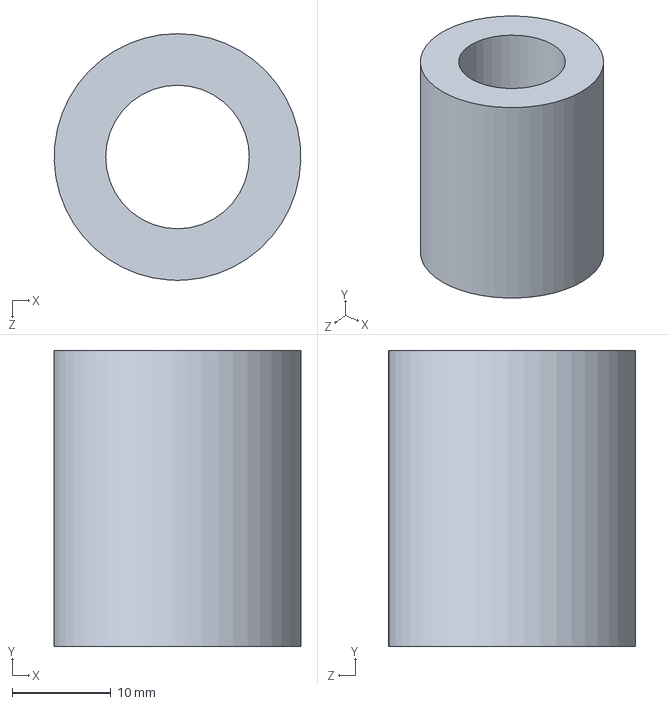
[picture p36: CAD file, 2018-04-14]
CAD Files/Cam-Follower SLDPARTS/Roller.SLDPRT
25.0 x 30.0 x 25.0 mm

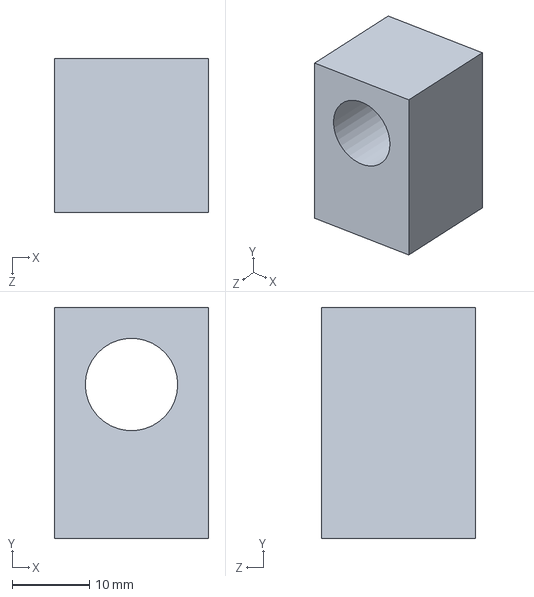
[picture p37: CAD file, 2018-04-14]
CAD Files/ViscousDashpotPartsAug2016/Dashpot_v2/lowerconnector.SLDPRT
20.0 x 30.0 x 20.0 mm

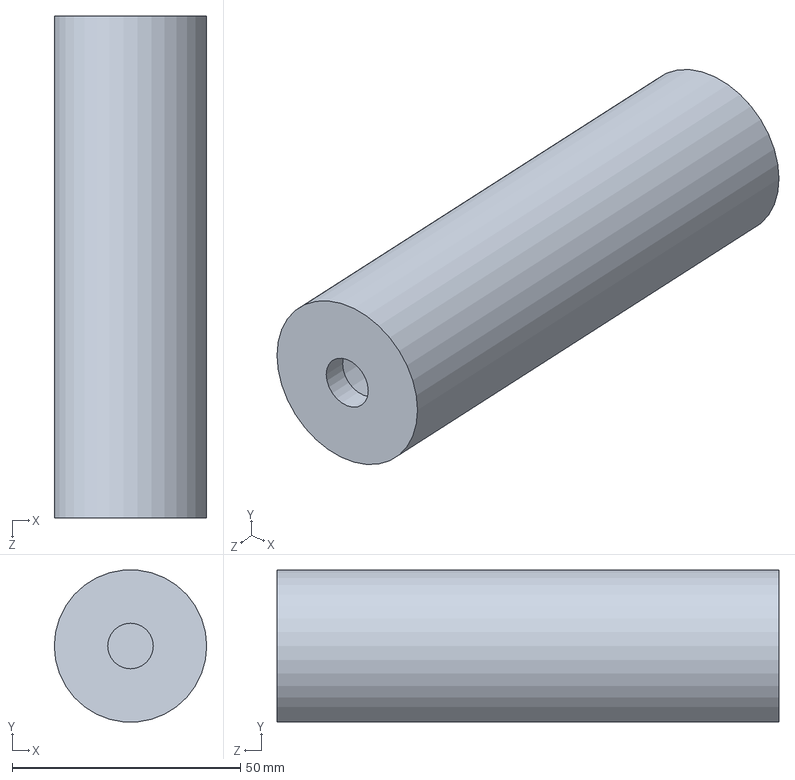
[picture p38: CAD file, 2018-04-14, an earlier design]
CAD Files/ViscousDashpotPartsAug2016/Dashpot_v1/HollowCylinder.SLDPRT
33.4 x 33.3 x 110.0 mm

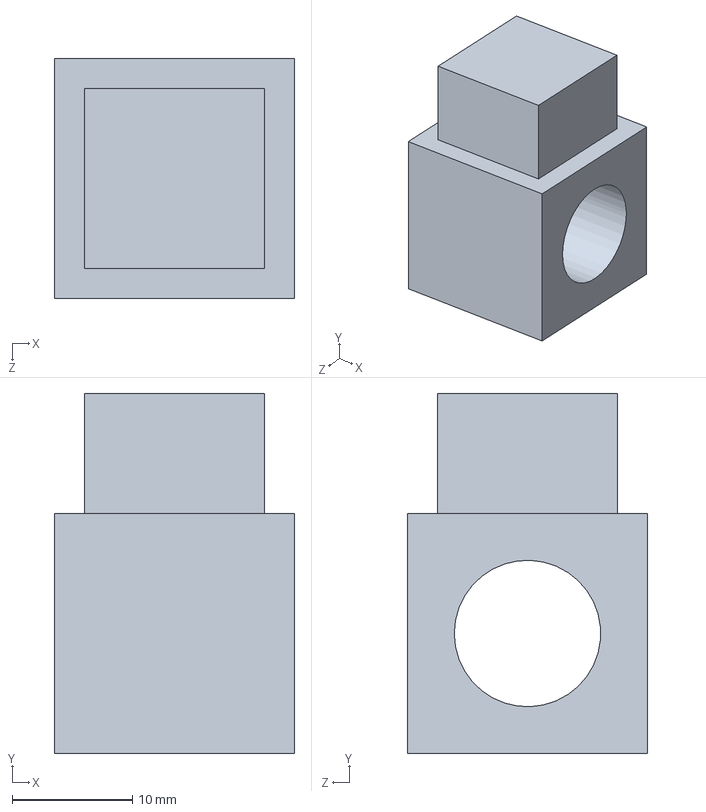
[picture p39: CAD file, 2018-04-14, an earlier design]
CAD Files/ViscousDashpotPartsAug2016/Dashpot_v1/BracketConnectorLower.SLDPRT
20.0 x 30.0 x 20.0 mm

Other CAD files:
CAD Files/ViscousDashpotPartsAug2016/Dashpot_v1/Piston.SLDPRT
CAD Files/ViscousDashpotPartsAug2016/Dashpot_v1/BracketConnector.SLDPRT
